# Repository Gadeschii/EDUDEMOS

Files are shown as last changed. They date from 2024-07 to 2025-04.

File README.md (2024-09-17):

# Arduino Temperature, Humidity, Light, and Voltage Control Project

This Arduino project reads temperature and humidity values, controls LEDs based on temperature, uses Light Dependent Resistors (LDRs) to control a servo motor, and measures the voltage of a DC
## Components Used

- ESP32 Board
- Temperature and Humidity Sensor (e.g., DHT11/DHT22)
- LEDs (3 different colors for Cold, Good, and Heat indicators)
- Light Dependent Resistors (LDRs)
- Servo Motor
- Adafruit IO for data logging

## Pin Configuration

- `ledPin1Cold`: Pin connected to the LED indicating cold temperature.
- `ledPin2Good`: Pin connected to the LED indicating good temperature.
- `ledPin3Heat`: Pin connected to the LED indicating high temperature.
- `ldrPin1`: Pin connected to the first LDR.
- `ldrPin2`: Pin connected to the second LDR.
- `myServo`: Pin connected to the servo motor.

## Code Explanation
## Method Explanations

### setup()

Initializes the serial communication, sets up the WiFi connection, OTA updates, DHT sensor, LEDs, and servo motor. It also creates FreeRTOS tasks for reading sensor data and voltage.

### loop()

Handles OTA updates and maintains the connection to Adafruit IO.

### readVoltage()

Reads the voltage from a DC motor using a voltage sensor, converts it to microvolts, and sends the data to Adafruit IO. It takes multiple readings to reduce noise and applies a minimum threshold to filter out noise.

### readSensorTask1(void * parameter)

A FreeRTOS task that periodically reads and processes temperature and humidity data from the DHT sensor. It sends the data to Adafruit IO and controls the LEDs based on the temperature.

### readSensorTask2(void * parameter)

A FreeRTOS task that periodically reads values from two LDRs, calculates the difference, and adjusts the servo motor based on the light difference. It also sends the average LDR values to Adafruit IO.

### readVoltageTask(void * parameter)

A FreeRTOS task that periodically reads and processes the voltage from a DC motor. It sends the voltage data to Adafruit IO.

### setupWiFi()

Connects the ESP32 to a WiFi network and maintains the connection to Adafruit IO.

### setupOTA()

Initializes ArduinoOTA for over-the-air updates and defines OTA event handlers.

### handleOTA()

Handles OTA updates by calling `ArduinoOTA.handle()`.

### setupDHT()

Initializes the DHT sensor.

### setupLEDsAndServo()

Sets up the pins for the LEDs and attaches the servo motor to its pin.

### updateSensorData()

Reads temperature and humidity values from the DHT sensor, sends the data to Adafruit IO, and controls the LEDs based on the temperature.

### updateLDRAndServo()

Reads values from two LDRs, calculates the difference, adjusts the servo motor based on the light difference, and sends the average LDR values to Adafruit IO.

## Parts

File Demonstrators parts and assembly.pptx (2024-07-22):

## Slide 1

GRADO EN INGENIERÍA EN DISEÑO INDUSTRIAL
Y DESARROLLO DE PRODUCTOS

Proyecto ERASMUS +

EDUcating through Sustainable DEMOnstrators

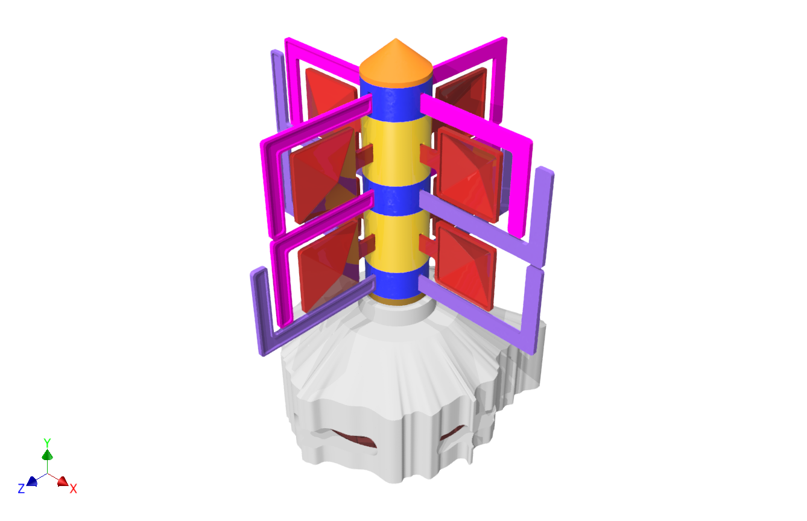
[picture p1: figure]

TRABAJO DE FIN DE GRADO
26 DE JUNIO DE 2024

Autora: Patricia Er López Marrero
Tutor 1: Pedro Manuel Hernández Castellano
Tutora 2: Annabella Narganes Pineda

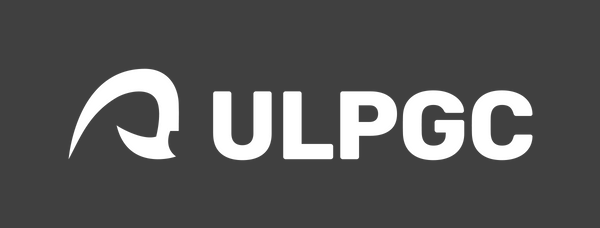
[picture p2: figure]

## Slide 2

1

2

3.5

4

5

Wind Demonstartor

33 pieces

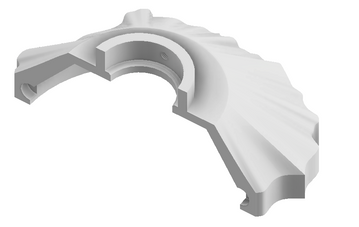
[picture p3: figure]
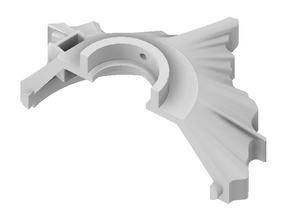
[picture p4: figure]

x2

x3

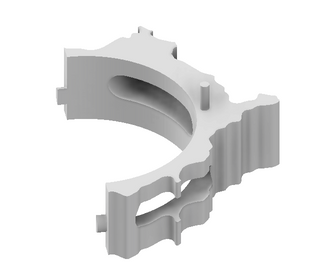
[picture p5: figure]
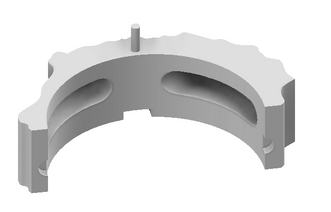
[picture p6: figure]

Cylinders

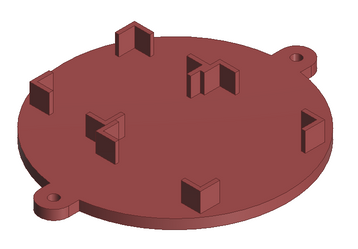
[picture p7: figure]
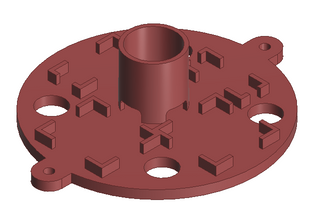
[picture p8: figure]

x8

x6

x6

Base with electronics

Blades


217 mm

259 mm

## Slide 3

Assembly


Base assembly

Cylinders assembly

Wood joints

Blades - cylinders assembly

Top view

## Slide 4

1


166 mm

2

3.5

4

5

Water + Solar Demonstrator

21 pieces


Base with electronics

Solar parts

x8


x2

x2

Water parts

250 mm

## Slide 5

Assembly

Condensation


Solar parts assembly

Cylinders assembly


Leaf - cylinder assembly

Top view

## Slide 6

Prototypes with electronics

Combine


Half section view of the base


Bearing

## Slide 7

Other element specifications

Bearing ZZ type

exterior Ø 40 mm

interior Ø 17 mm

Height 12 mm

1 unit


Wood joints

Ø 8 mm

Height 40 mm

3 units

Aluminum foil tape


1 unit

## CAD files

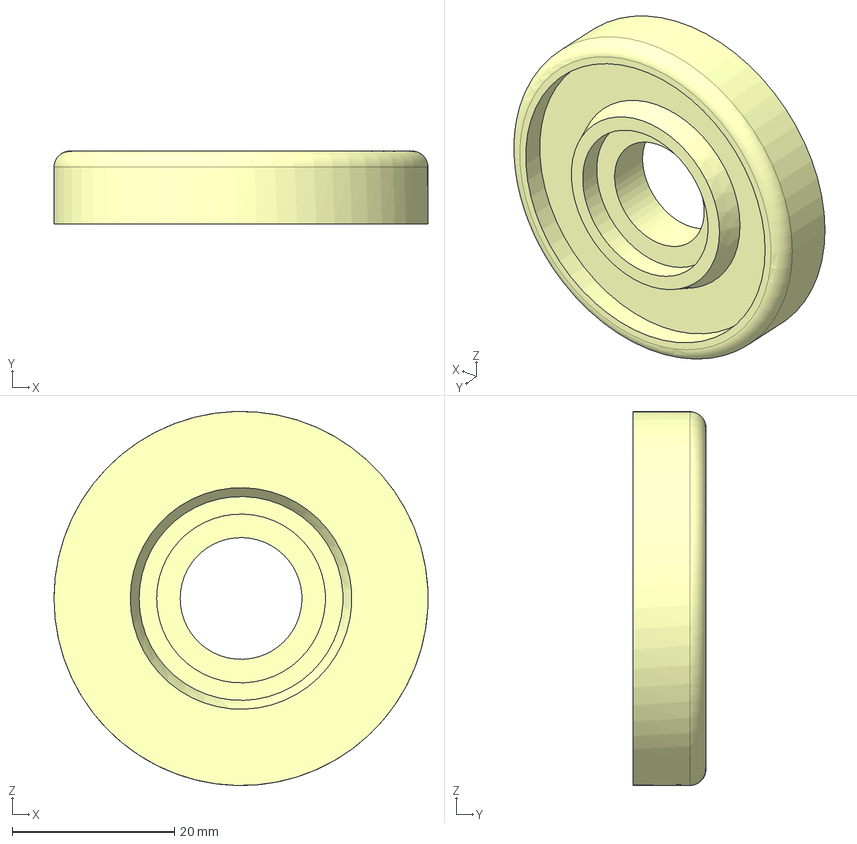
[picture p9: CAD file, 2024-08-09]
3d-files/stp-files/Water static disc_V2_x2.stp
46.1 x 9.00 x 46.1 mm

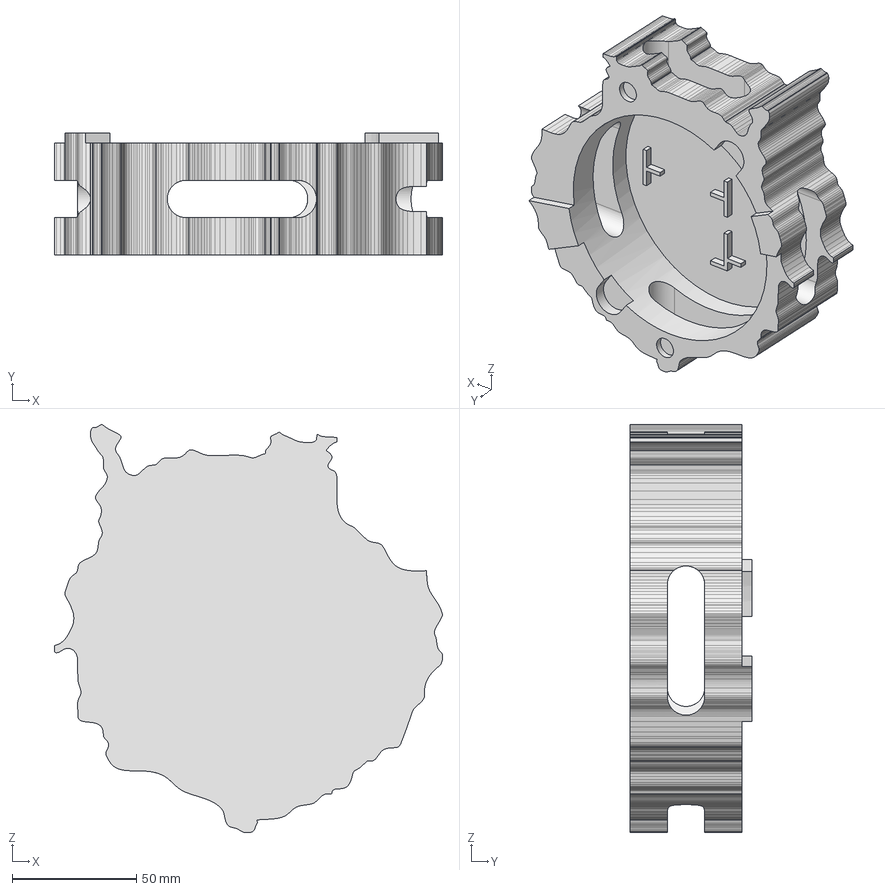
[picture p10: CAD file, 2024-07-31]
3d-files/stp-files/Base_V3_x1.stp
156.1 x 49.0 x 164.1 mm

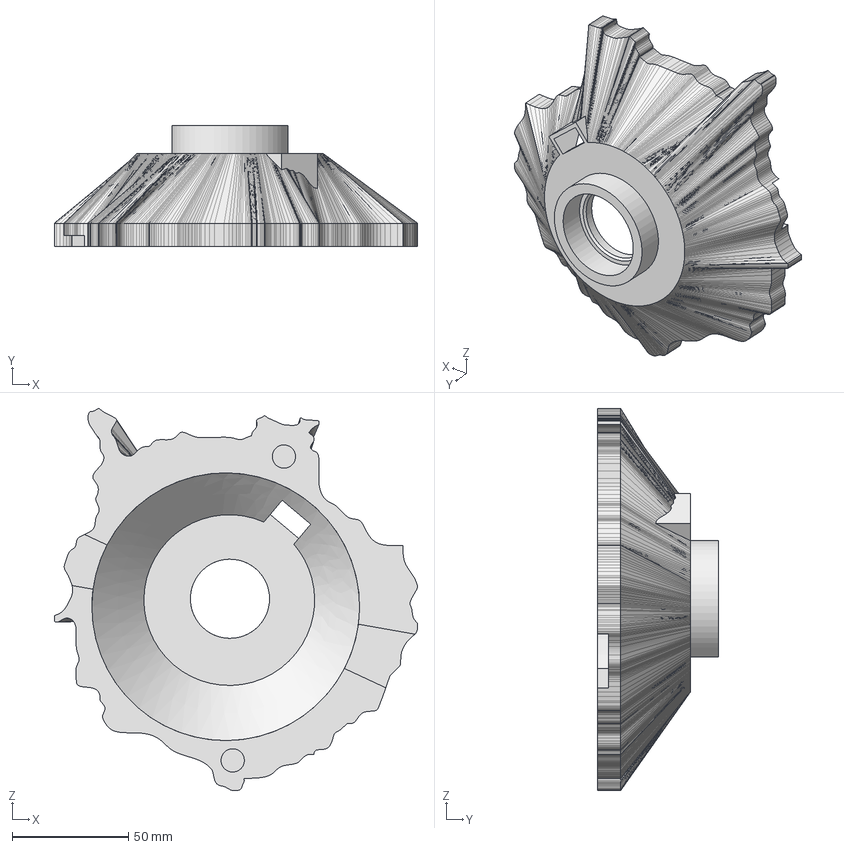
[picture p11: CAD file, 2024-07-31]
3d-files/stp-files/Base top_V3_x1.stp
156.1 x 52.0 x 164.1 mm

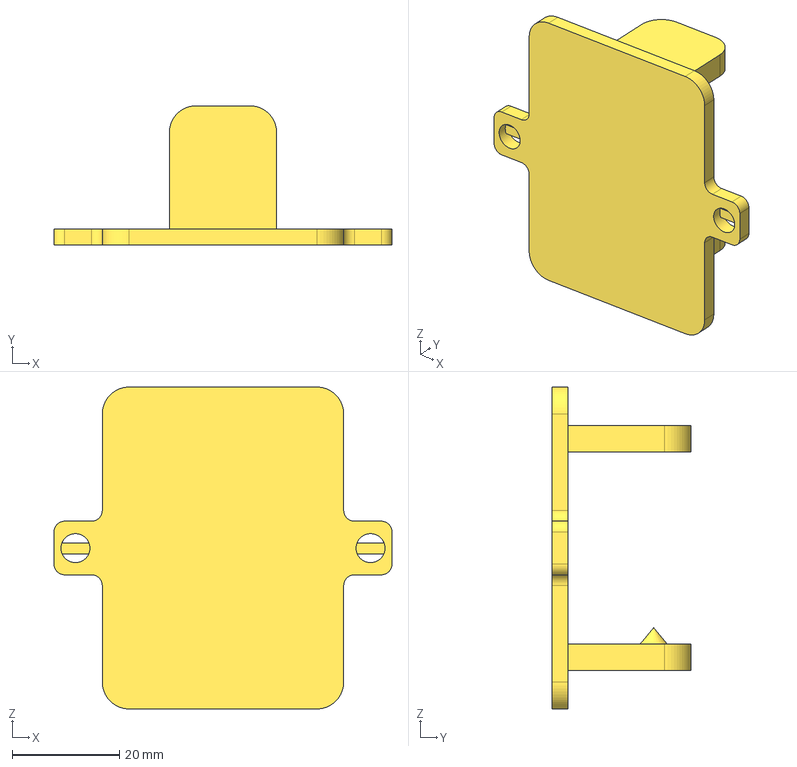
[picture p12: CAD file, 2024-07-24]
3d-files/stp-files/Solar panel spin_V2_x1.stp
63.0 x 26.0 x 60.0 mm

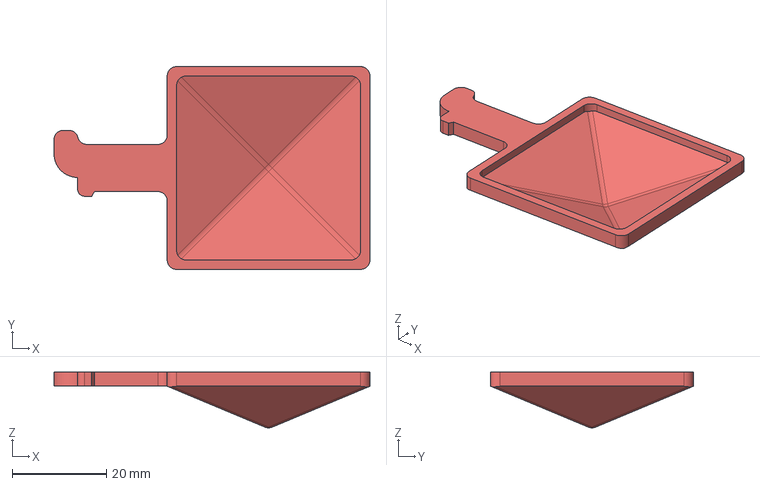
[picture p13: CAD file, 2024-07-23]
3d-files/stp-files/Square blade_x8.stp
67.0 x 43.0 x 11.8 mm

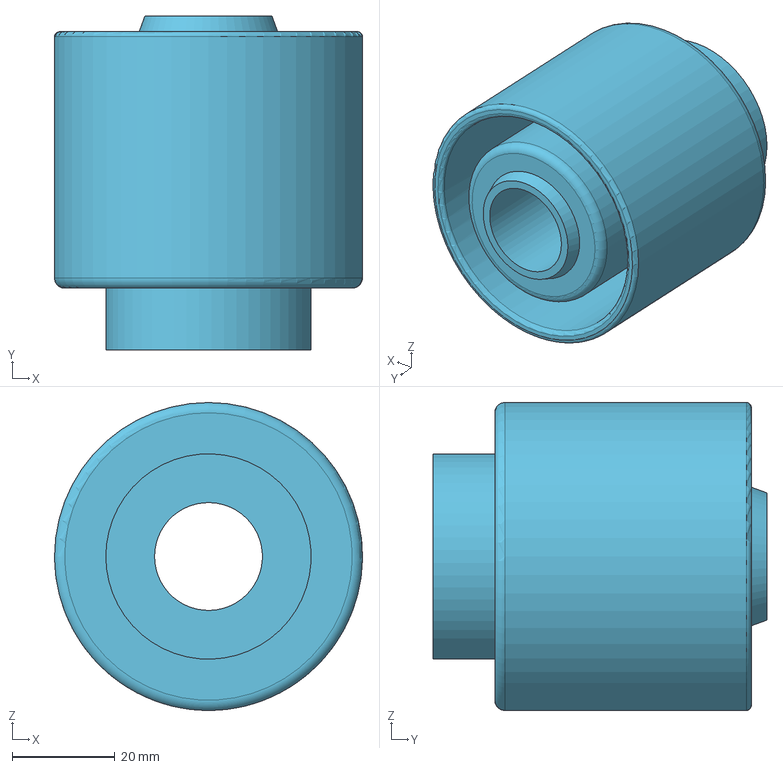
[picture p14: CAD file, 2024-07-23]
3d-files/stp-files/Water container_x1.stp
60.0 x 65.0 x 60.0 mm

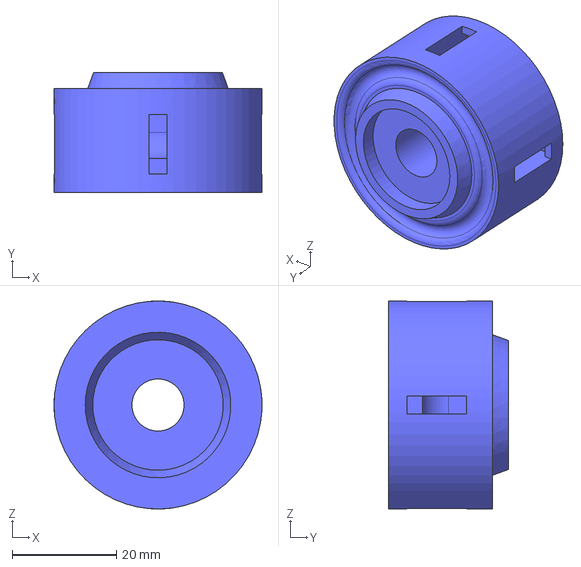
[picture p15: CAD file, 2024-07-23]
3d-files/stp-files/Small disc_x3.stp
40.0 x 23.0 x 40.0 mm

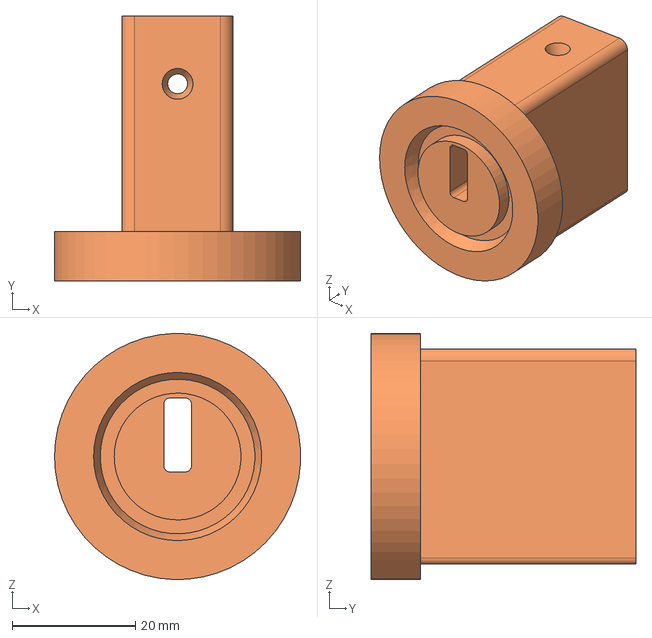
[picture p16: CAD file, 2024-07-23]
3d-files/stp-files/Solar static disc_x1.stp
40.0 x 43.0 x 40.0 mm

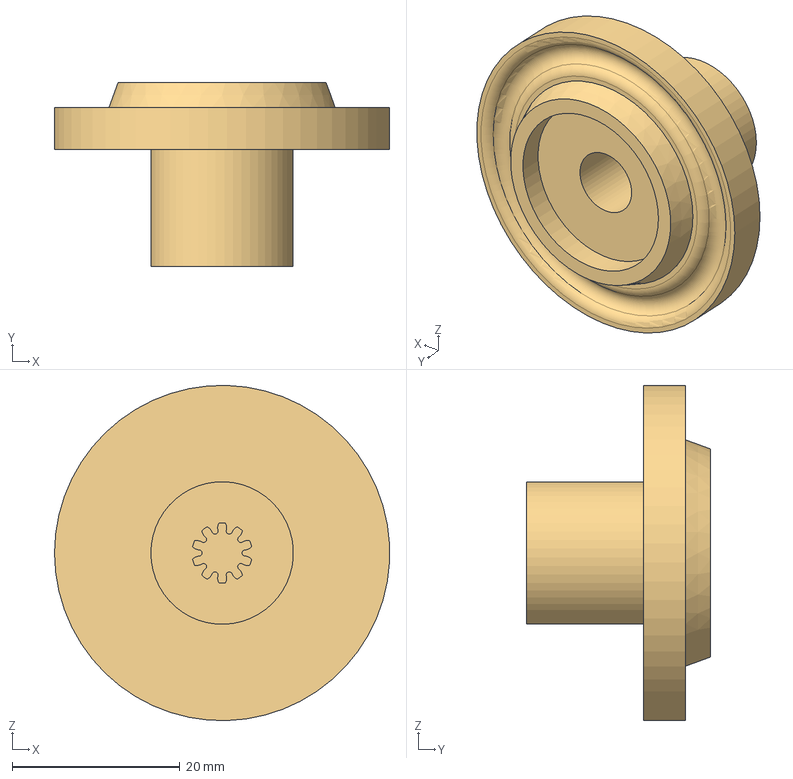
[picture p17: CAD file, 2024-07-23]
3d-files/stp-files/Wind bearing disc_x1.stp
40.0 x 22.0 x 40.0 mm

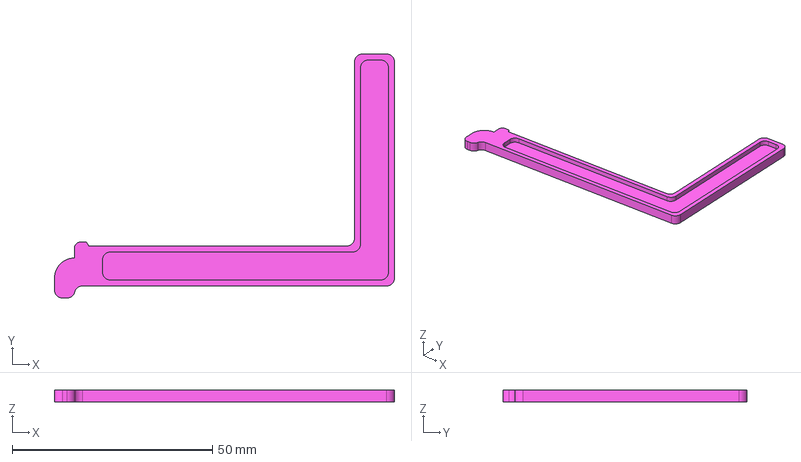
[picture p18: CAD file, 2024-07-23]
3d-files/stp-files/Small L blade_x6.stp
85.0 x 61.0 x 3.00 mm

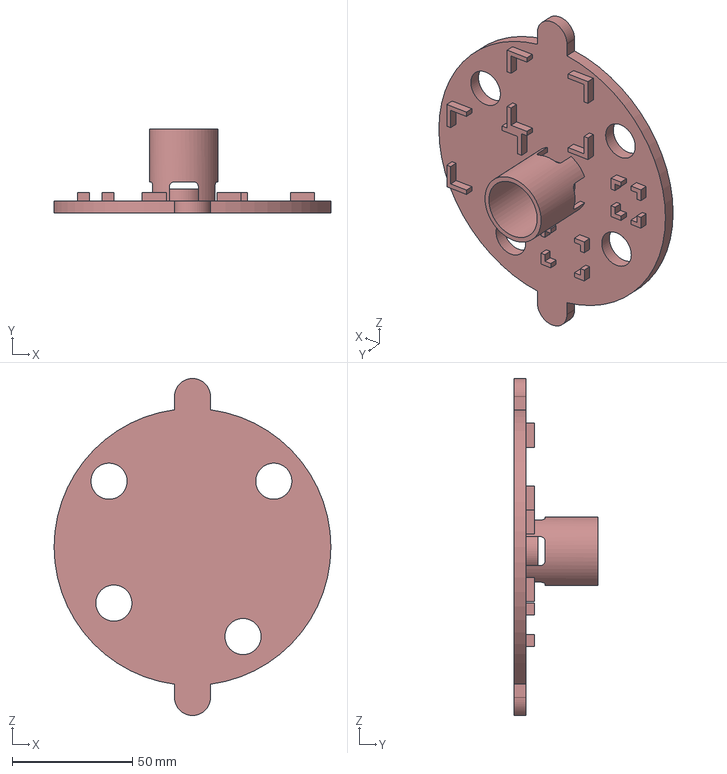
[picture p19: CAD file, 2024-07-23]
3d-files/stp-files/Base middle_x1.stp
115.0 x 35.0 x 140.0 mm

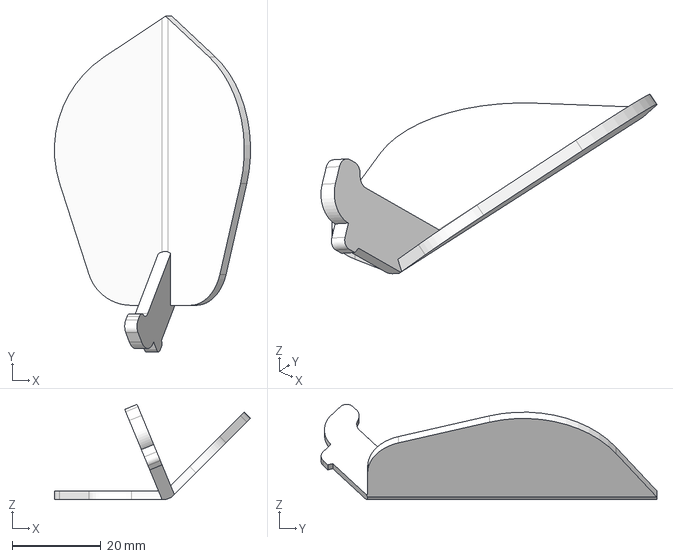
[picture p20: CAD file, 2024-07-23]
3d-files/stp-files/Leaf_x8.stp
44.1 x 75.4 x 21.4 mm

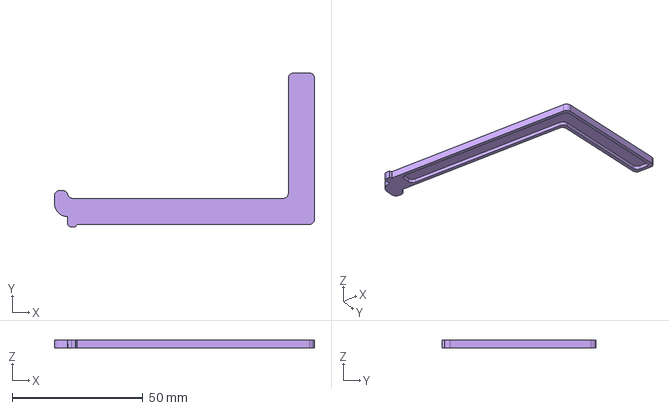
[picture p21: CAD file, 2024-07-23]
3d-files/stp-files/Big L blade_x6.stp
99.5 x 59.0 x 3.00 mm

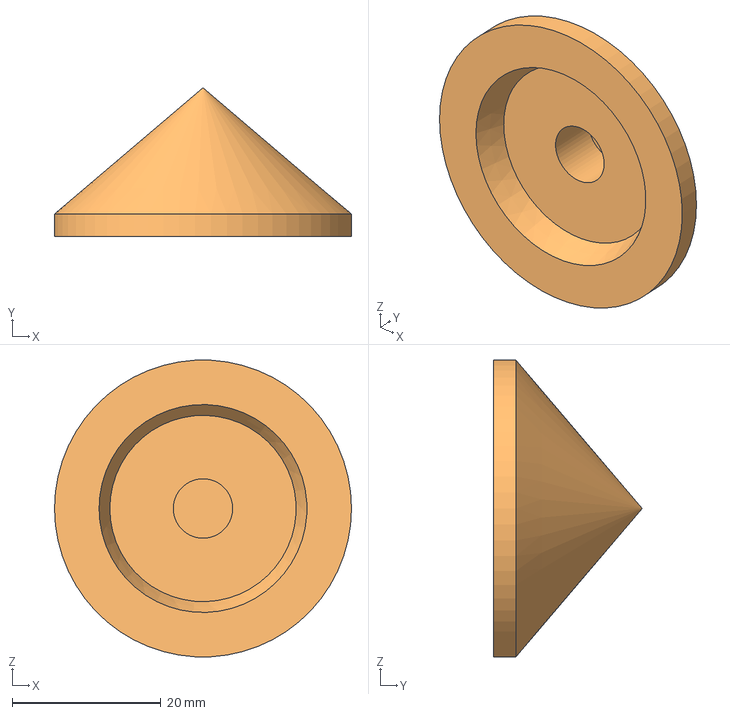
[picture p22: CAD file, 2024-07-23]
3d-files/stp-files/Top_x1.stp
40.0 x 20.0 x 39.9 mm

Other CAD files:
3d-files/stp-files/Big disc_x2.stp
3d-files/stp-files/Base_V2_x1.stp
3d-files/stp-files/Base top_V2_x1.stp
3d-files/stp-files/Base_x1.stp
3d-files/stp-files/Base top_x1.stp
3d-files/stp-files/Solar panel spin_x1.stp
3d-files/stp-files/Water static disc_x2.stp

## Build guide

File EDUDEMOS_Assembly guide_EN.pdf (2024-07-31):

# 3 x 1 Convertible demonstrator

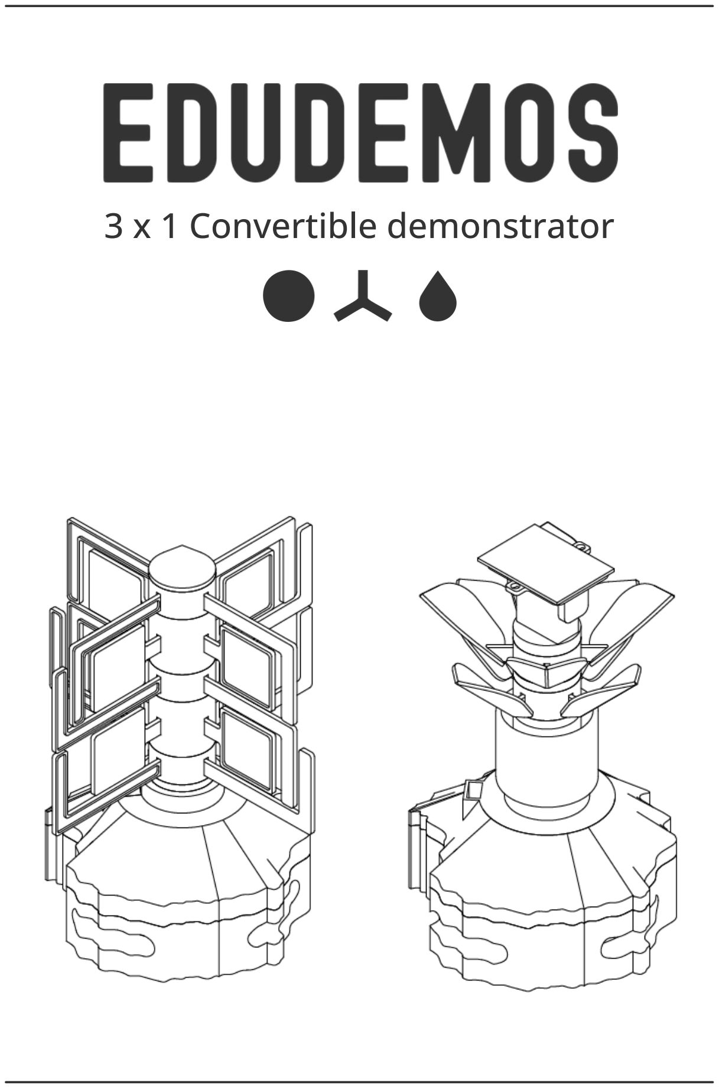
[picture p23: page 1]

# 3x1 Demonstrator

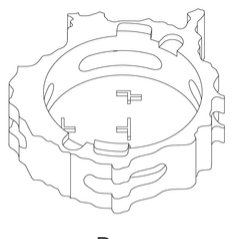
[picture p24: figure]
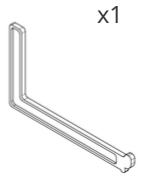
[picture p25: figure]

Bearing | Wood joints
x1 | x3

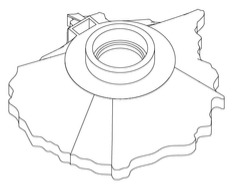
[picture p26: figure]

Big L blade | Square blade | Small L blade
x6 | x8 | x6

Leaf
x8

## Elements

Base | Middle base | Top base
x1 | x1 | x1
Big disc | Small disc Bearing disc | Top
x2 | x3 | x1 | x1

Static disc
x2

Water container
x1

Solar spin
x1

Solar disc
x1

## Total 47 elements

# Wind demonstrator

## Assembly guide

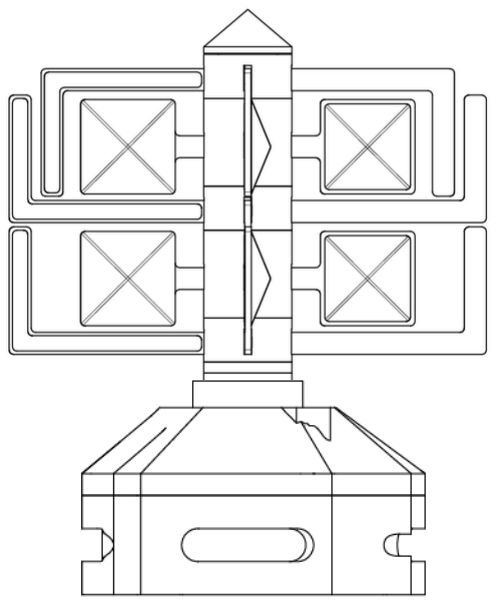
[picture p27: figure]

# Wind demonstrator

## Elements

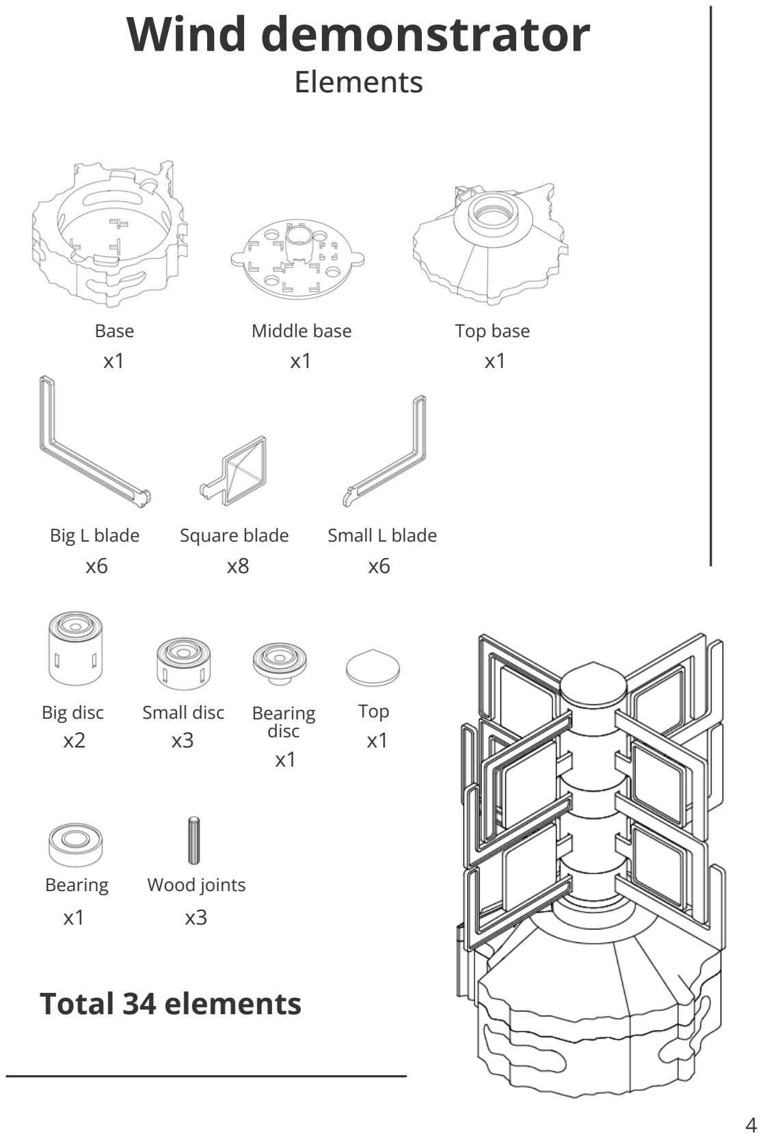
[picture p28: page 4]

Bearing | Wood joints
Big L blade | Square blade | Small L blade
Base | Middle base | Top base
x1 | x1 | x1
x6 | x8 | x6
Big disc | Small disc Bearing disc

Top
x2 | x3 x1

x1

x1 | x3

## Total 34 elements

# Wind demonstrator

## Core assembly

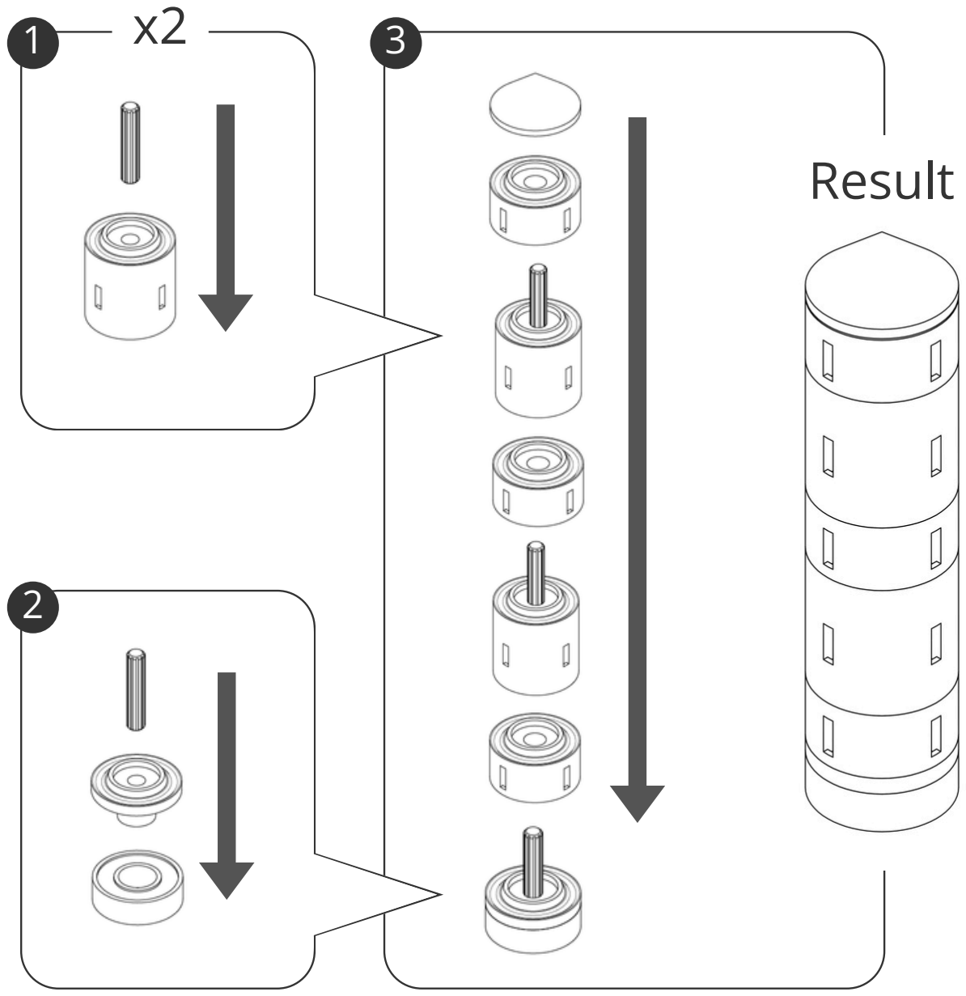
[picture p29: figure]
Result

The two big discs should move together, while each small discs should move individually.
If needed, take out a little bit the big discs from the wood joints in order to reduce friction.

6

## Blades assembly

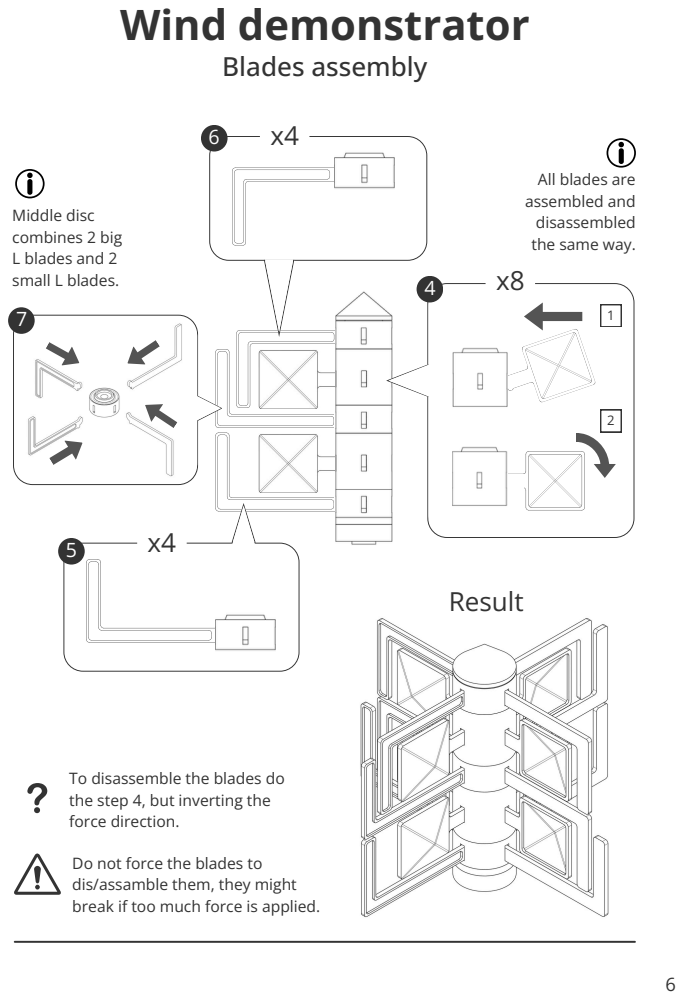
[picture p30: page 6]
Wind demonstrator; Middle disc combines 2 big L blades and 2 small L blades.; Result

All blades are
assembled and
disassembled
the same way.

To disassemble the blades do
the step 4, but inverting the
force direction.

Do not force the blades to
dis/assamble them, they might
break if too much force is applied.

# Wind demonstrator

## Base assembly

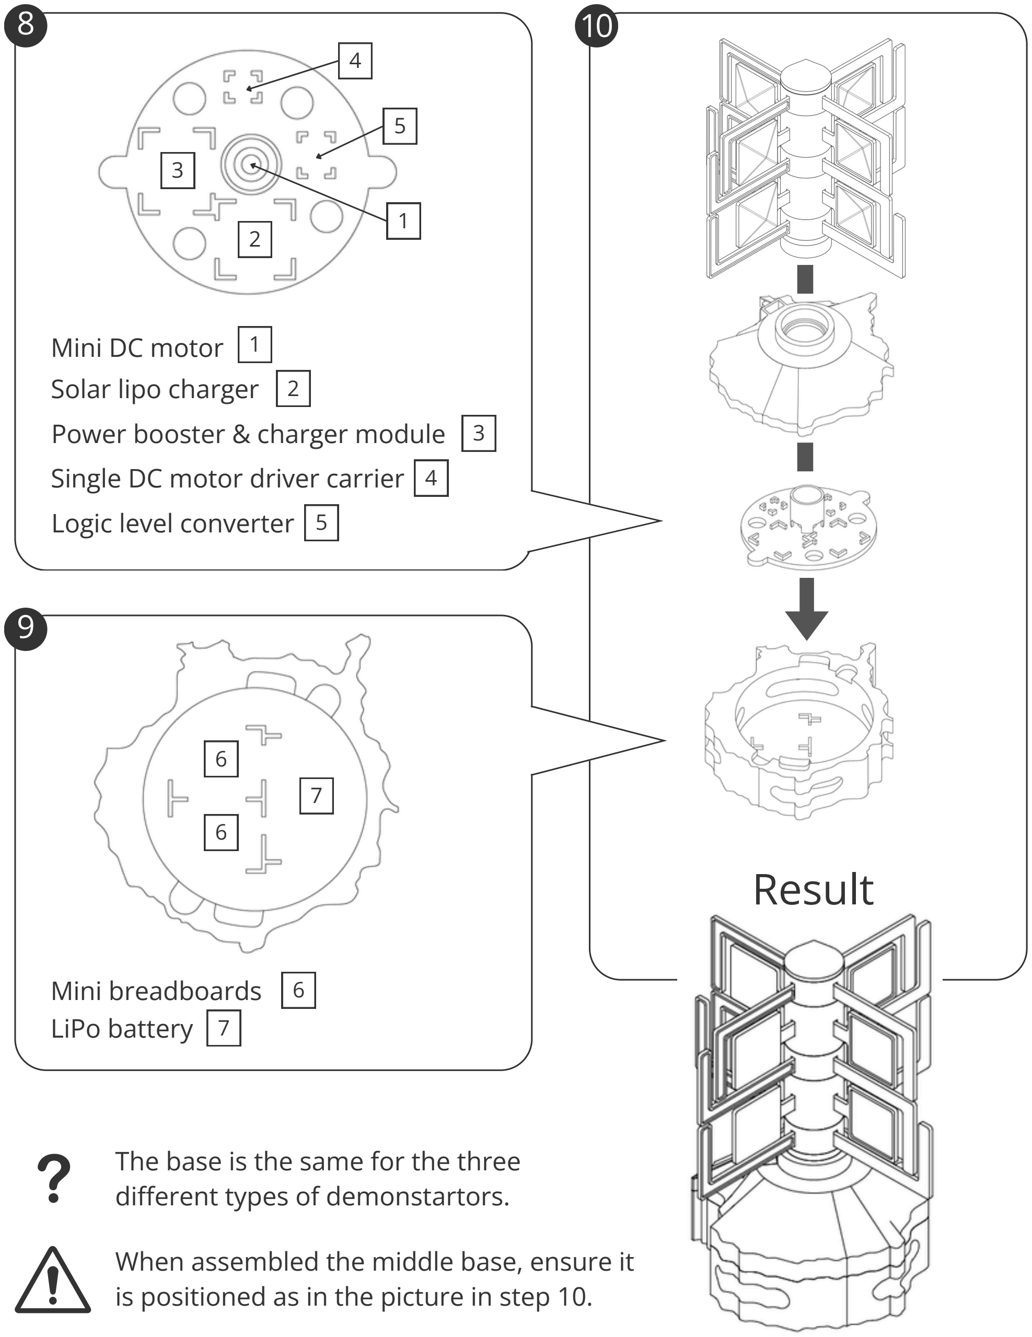
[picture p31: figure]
Mini breadboards LiPo battery; Mini DC motor; The base is the same for the three different types of demonstartors.; Power booster & charger module; Solar lipo charger; Logic level converter; Single DC motor driver carrier; Result

When assembled the middle base, ensure it is positioned as in the picture in step 10.

# Solar + Water demonstrator

## Assembly guide

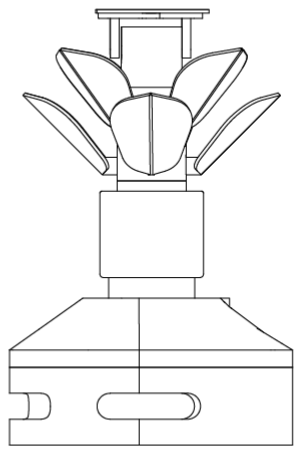
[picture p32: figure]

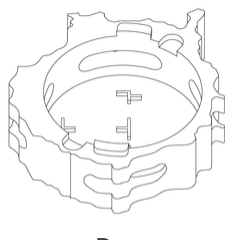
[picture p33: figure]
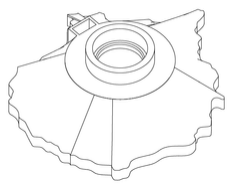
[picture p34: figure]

Base | Middle base | Top base
x1 | x1 | x1

# Solar + Water demonstrator

## Elements

Small disc
x3

Water container
x1

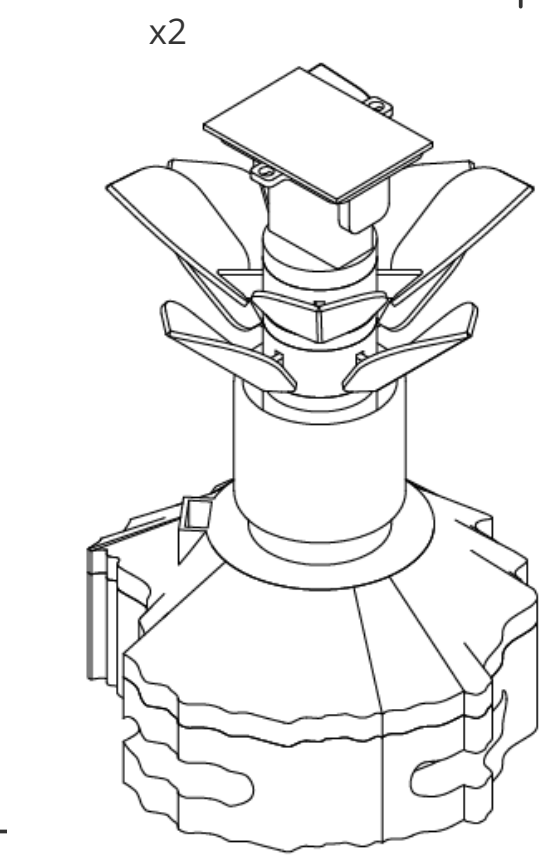
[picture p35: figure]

Solar spin
x1

Solar disc
x1

Leaf
x8

Static disc

Water demonstrator

Solar demonstrator

## Total 19 elements

## Core assembly

1 | 3

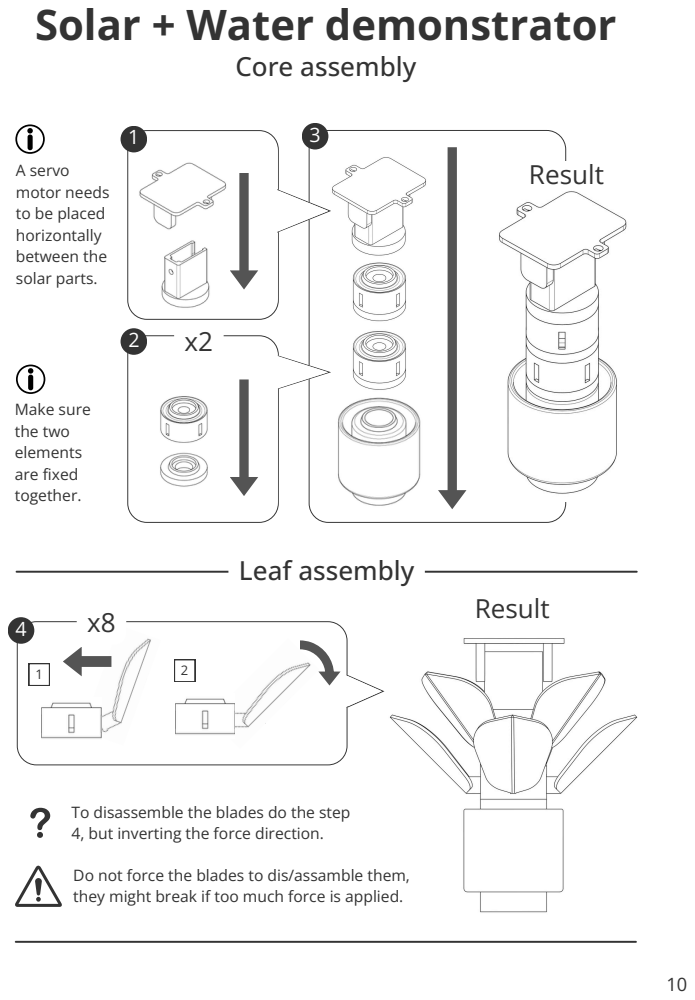
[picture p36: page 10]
Result; Leaf assembly; Make sure the two elements are fixed together.

Solar + Water demonstrator

A servo
motor needs
to be placed
horizontally
between the
solar parts.

To disassemble the blades do the step
4, but inverting the force direction.

Do not force the blades to dis/assamble them,
they might break if too much force is applied.

5

## Base assembly

See page 7 for the base assembly instructions.

# Solar + Water demonstrator

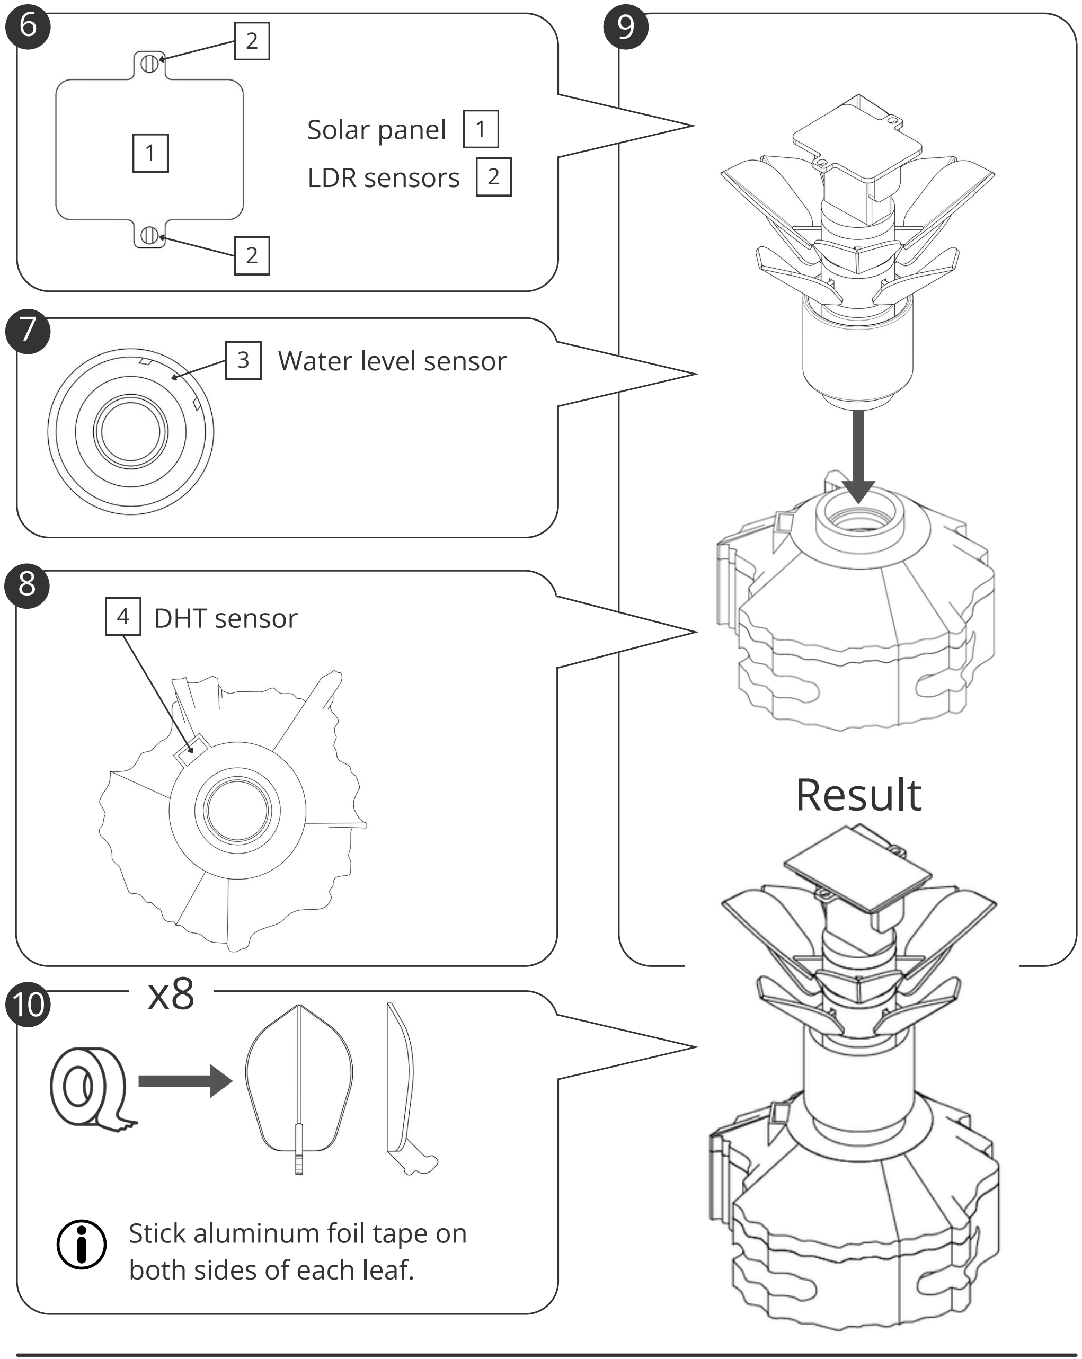
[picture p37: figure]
DHT sensor; Solar panel; Stick aluminum foil tape on both sides of each leaf.; Result; LDR sensors; Water level sensor

## Personalise your own demonstrator

# What else can you imagine?

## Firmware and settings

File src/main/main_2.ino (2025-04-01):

/*                                                                                                           *
 *  Thank you for building EduDemoS!                                                                         *
 *                                                                                                           *
 *  This file is part of the EduDemoS Project and is licensed under the Creative Commons Attribution         *
 *  NonCommercial ShareAlike 4.0 International license (CC BY-NC-SA 4.0). For full license details, see the  *
 *  license.txt file or visit https://creativecommons.org/licenses/by-nc-sa/4.0/                             *     
 *                                                                                                           *
 *  EduDemoS is co-funded by the European Union. You can find more information at edudemos.eu                *                                                         
 *                                                                                                           *
 *  +-----------------------------------------------------------------------------------------------------+  *            
 */

//include the necesary libraries
#include <WiFi.h>
#include <WiFiClient.h>
#include <HTTPClient.h>
#include <ArduinoJson.h>
#include "AdafruitIO_WiFi.h"
#include "DHT.h"
#include <ESP32Servo.h>
#include <ArduinoOTA.h>
//#include "config.h"

// Pin definitions and constants
#define DHTPIN 32
#define DHTTYPE DHT11
#define ledPin1Cold 5
#define ledPin2Good 18
#define ledPin3Heat 19
#define ldrPin1 34
#define ldrPin2 35
#define servoPin 25
#define DcMotorPin 39
#define SolarPin 36
#define SENSOR_INTERVAL_10_SEC 10000
#define OFFSET 550
#define OFFSETLDR 300 //Difference between LDR1 and LDR2, (each case are different), look for yor personal value

/************************ Adafruit IO Config *******************************/
#define IO_USERNAME "IO_USERNAME"
#define IO_KEY "IO_KEY"

/******************************* WIFI **************************************/
#define WIFI_SSID "WIFI_SSID"
#define WIFI_PASS "WIFI_PASS"

WiFiServer telnetServer(23); 
WiFiClient telnetClient;

// Voltage divider resistances definitions
const float R1 = 1000.0; // 1kΩ resistor
const float R2 = 1000.0; // 1kΩ resistor

// Global variables
DHT dht(DHTPIN, DHTTYPE);
Servo myServo;

// Variables to store LDR sensor readings
int ldrValue1 = 0;
int ldrValue2 = 0;
int averageLdrValue = 0;

// Variables to store water sensor readings
const int WaterSensorPin = 39; // // Analog Value from VN PIN
int sensorValue = 0; // Analog Value filter

// Servo configuration variables
int servoPos = 100;  // Initial servo position in the middle (90 degrees)
int servoStep = 10;  // Servo movement increment/decrement
int tolerance = 150; // Tolerance to avoid small movements

AdafruitIO_WiFi io(IO_USERNAME, IO_KEY, WIFI_SSID, WIFI_PASS);
AdafruitIO_Feed *temperature = io.feed("temperature");
AdafruitIO_Feed *humidity = io.feed("humidity");
AdafruitIO_Feed *ldrFeed = io.feed("ldr");
//AdafruitIO_Feed *ldr1Feed = io.feed("ldr1Feed");
//AdafruitIO_Feed *ldr2Feed = io.feed("ldr2Feed");
AdafruitIO_Feed *waterLevelFeed = io.feed("waterLevel");
AdafruitIO_Feed *microvoltsMotorDcFeed = io.feed("microvoltsMotorDc");
AdafruitIO_Feed *microvoltsSolarFeed = io.feed("microvoltsSolar");
AdafruitIO_Feed *ledHighFeed =  io.feed("ledHighFeed");
AdafruitIO_Feed *ledGoodFeed =  io.feed("ledGoodFeed");
AdafruitIO_Feed *ledColdFeed =  io.feed("ledColdFeed");
AdafruitIO_Feed *wifiFeed =  io.feed("wifiFeed");
float lastMicrovolts = 0;

void setup() {
  Serial.begin(115200); // Start serial communication at 115200 baud rate
  analogReadResolution(12); // ESP32 has a 12-bit ADC
  analogSetAttenuation(ADC_11db); // Set attenuation for higher sensitivity
  pinMode(4, INPUT);

  //setupWiFi(); // Setup WiFi connection
  //setupOTA(); // Setup OTA for remote updates
  setupDHT(); // Setup DHT sensor
  setupLEDsAndServo(); // Setup LED pins and servo

  // Create tasks
  xTaskCreatePinnedToCore(
    readSensorTask1,   // Task function
    "ReadSensorTask1", // Name of the task
    4096,             // Stack size
    NULL,              // Task input parameter
    1,                 // Priority of the task
    NULL,              // Task handle
    0                  // Core where the task should run
  );

  xTaskCreatePinnedToCore( 
    readSensorTask2,   // Task function
    "ReadSensorTask2", // Name of the task
    4096,             // Stack size
    NULL,              // Task input parameter
    1,                 // Priority of the task
    NULL,              // Task handle
    1                  // Core where the task should run
  );

  xTaskCreatePinnedToCore(
    readSensorTask3,   // Task function
    "ReadSensorTask3", // Name of the task
    4096,             // Stack size
    NULL,              // Task input parameter
    1,                 // Priority of the task
    NULL,              // Task handle
    1                  // Core where the task should run
  );

  xTaskCreatePinnedToCore(
    readDcMotorVoltageTask,   // Task function
    "readDcMotorVoltageTask", // Name of the task
    4096,             // Stack size
    NULL,              // Task input parameter
    1,                 // Priority of the task
    NULL,              // Task handle
    1                  // Core where the task should run
  );

  xTaskCreatePinnedToCore(
    readSolarVoltageTask,   // Task function
    "readSolarVoltageTask", // Name of the task
    4096,             // Stack size
    NULL,              // Task input parameter
    1,                 // Priority of the task
    NULL,              // Task handle
    1                  // Core where the task should run
  );
}

void loop() {
  //handleOTA(); // Handle OTA updates
  //io.run(); // Maintain connection to Adafruit IO
}

void setupWiFi() {
  int retries = 0;
  const int maxRetries = 5;

  WiFi.begin(WIFI_SSID, WIFI_PASS);
  Serial.print("Connecting to WiFi");

  while (WiFi.status() != WL_CONNECTED && retries < maxRetries) {
    delay(1000);
    Serial.print(".");
    retries++;
  }

  if (WiFi.status() == WL_CONNECTED) {
    Serial.println("\nConnected to WiFi");
    // Send microvolts to Adafruit IO
    wifiFeed->save(WIFI_SSID);
  } else {
    Serial.println("\nWiFi connection failed. Restarting...");
    ESP.restart();
  }

  connectToAdafruitIO();
}

void connectToAdafruitIO() {
  Serial.print("Connecting to Adafruit IO");
  io.connect();

  int retries = 0;
  const int maxRetries = 5;

  while (io.status() < AIO_CONNECTED && retries < maxRetries) {
    Serial.print(".");
    delay(500);
    retries++;
  }

  if (io.status() < AIO_CONNECTED) {
    Serial.println("\nFailed to connect to Adafruit IO. Restarting...");
    ESP.restart();
  }

  Serial.println("\nConnected to Adafruit IO");
}

void setupOTA() {
  // Start telnet server
  telnetServer.begin();
  telnetServer.setNoDelay(true);
  // Initialize ArduinoOTA for over-the-air updates
  ArduinoOTA.setHostname("ESP32-OTA");
  ArduinoOTA.setPassword("admin"); // Uncomment to set a password for OTA updates
  // Define OTA event handlers
  ArduinoOTA.onStart([]() {
    String type;
    if (ArduinoOTA.getCommand() == U_FLASH) {
      type = "sketch";
    } else { // U_SPIFFS
      type = "filesystem";
    }
    Serial.println("Start updating " + type);
  });
  ArduinoOTA.onEnd([]() {
    Serial.println("\nOTA Update Finished");
  });
  ArduinoOTA.onProgress([](unsigned int progress, unsigned int total) {
    Serial.printf("Progress: %u%%\r", (progress / (total / 100)));
  });
  ArduinoOTA.onError([](ota_error_t error) {
    Serial.printf("Error[%u]: ", error);
    if (error == OTA_AUTH_ERROR) {
      Serial.println("Auth Failed");
    } else if (error == OTA_BEGIN_ERROR) {
      Serial.println("Begin Failed");
    } else if (error == OTA_CONNECT_ERROR) {
      Serial.println("Connect Failed");
    } else if (error == OTA_RECEIVE_ERROR) {
      Serial.println("Receive Failed");
    } else if (error == OTA_END_ERROR) {
      Serial.println("End Failed");
    }
  });
  ArduinoOTA.begin(); // Start the OTA service
  Serial.println("OTA Ready");
}

void handleOTA() {
  ArduinoOTA.handle(); // Handle OTA updates

  //check if there are new client
  // Verificar si hay un nuevo cliente telnet
  if (telnetServer.hasClient()) {
    if (!telnetClient || !telnetClient.connected()) {
      if (telnetClient) telnetClient.stop();
      telnetClient = telnetServer.available();
      Serial.println("New Telnet client connected");
    } else {
      telnetServer.available().stop();
    }
  }

  //Send data to the telnet client server
  if (telnetClient && telnetClient.connected()) {
    while (Serial.available()) {
      telnetClient.write(Serial.read());
    }
    while (telnetClient.available()) {
      Serial.write(telnetClient.read());
    }
  }

}
void setupDHT() {
  dht.begin(); // Start the DHT sensor
}

void setupLEDsAndServo() {
  pinMode(ledPin1Cold, OUTPUT);
  pinMode(ledPin2Good, OUTPUT);
  pinMode(ledPin3Heat, OUTPUT);
  // Attach the servo to the corresponding pin
  myServo.attach(servoPin);

  // Set the servo to the initial position (90 degrees, in the middle)
  myServo.write(servoPos);
}

void readSensorTask1(void * parameter) {
  for (;;) {
    Serial.println("----------------------- Measured Temperature / Humidity -----------------------  ");
    updateSensorData(); // Read and process sensor data 
    vTaskDelay(SENSOR_INTERVAL_10_SEC / portTICK_PERIOD_MS); // Delay for 5 minutes
  }
}

void readSensorTask2(void * parameter) {
  for (;;) {
    Serial.println("----------------------------- Measured LDR and Servo -----------------------------  ");
    updateLDRAndServo(); // Read LDR values and control servo
    vTaskDelay(SENSOR_INTERVAL_10_SEC / portTICK_PERIOD_MS); // Delay for 10 seconds
  }
}

void readSensorTask3(void * parameter) {
  for (;;) {
    Serial.println("----------------------------- Measured Water % -----------------------------  ");
    updateWater(); // Read LDR values and control servo
    vTaskDelay(SENSOR_INTERVAL_10_SEC / portTICK_PERIOD_MS); // Delay for 10 seconds
  }
}

void readSolarVoltageTask(void * parameter) {
  for (;;) {
    Serial.println("----------------------------- Measured Solar (V) ----------------------------  ");
    readSolarVoltage(); // Read and process voltage
    vTaskDelay(SENSOR_INTERVAL_10_SEC / portTICK_PERIOD_MS); // Delay for 10 seconds
  }
}

void readDcMotorVoltageTask(void * parameter) {
  for (;;) {
    Serial.println("----------------------------- Measured DC Motor (V) ----------------------------  ");
    readDcMotorVoltage(); // Read and process voltage
    vTaskDelay(SENSOR_INTERVAL_10_SEC / portTICK_PERIOD_MS); // Delay for 10 seconds
  }
}


void readDcMotorVoltage() {
  // Take multiple readings to reduce noise
  const int numReadings = 1000;
  unsigned long sum = 0;

  for (int i = 0; i < numReadings; i++) {
    int reading = analogRead(DcMotorPin);
    sum += reading;
  }

  float averageReading = sum / (float)numReadings;
  Serial.print("Average ADC reading: ");
  Serial.println(averageReading);  // Display the average value

  // Calculate voltage
  float voltage = (averageReading / 4095.0) * 3.3;  // For 12-bit ADC (0-4095)
  Serial.print("Measured voltage (V): ");
  Serial.println(voltage);  // Display the measured voltage

  // Adjust for voltage divider
  float inputVoltage = voltage / (R2 / (R1 + R2));

  // Convert to microvolts
  float microvoltsMotorDc = inputVoltage * 1000000.0;
  Serial.print("Input voltage (µV): ");
  Serial.println(microvoltsMotorDc);

  // Apply a minimum threshold to filter noise
  const float threshold = 10.0;  // Threshold in microvolts
  if (microvoltsMotorDc < threshold) {
    microvoltsMotorDc = 0;
  }

  // Check if the microvolts value has changed
  if (microvoltsMotorDc != lastMicrovolts) {
    Serial.print("Measured voltage: ");
    Serial.print(microvoltsMotorDc, 2);  // Display with 2 decimal places
    Serial.println(" µV");

    // Send microvolts to Adafruit IO
    microvoltsMotorDcFeed->save(microvoltsMotorDc);

    // Update the last microvolts value
    lastMicrovolts = microvoltsMotorDc;
  }
}

void readSolarVoltage() {
 int solarVoltagedV = analogRead ( SolarPin); //dV
 int solarVoltage = solarVoltagedV * 10;

  Serial.print("Voltage of Solar Panel: ");
  Serial.println(solarVoltage);  

  // Calculate voltage
  float voltage = (solarVoltage / 4095.0) * 3.3;  // For 12-bit ADC (0-4095)
  Serial.print("Measured voltage (V): ");
  Serial.println(voltage);  // Display the measured voltage

  // Convert to microvolts
  float microvoltsSolar = voltage * 1000000.0;
  Serial.print("Input voltage (µV): ");
  Serial.println(microvoltsSolar);

  // Apply a minimum threshold to filter noise
  const float threshold = 10.0;  // Threshold in microvolts
  if (microvoltsSolar < threshold) {
    microvoltsSolar = 0;
  }

  // Check if the microvolts value has changed
  if (microvoltsSolar != lastMicrovolts) {
    Serial.print("Send voltage: ");
    Serial.print(microvoltsSolar, 2);  // Display with 2 decimal places
    Serial.println(" µV");

    // Send microvolts to Adafruit IO
    microvoltsSolarFeed->save(microvoltsSolar);

    // Update the last microvolts value
    lastMicrovolts = microvoltsSolar;
  }
}

void updateSensorData() {
  // Read values from DHT sensor
  float h = dht.readHumidity();
  float t = dht.readTemperature();

  // Check if readings are valid
  if (isnan(h) || isnan(t)) {
    Serial.println("Failed to read from DHT sensor!");
    return;
  }

  // Send values to Adafruit IO
  temperature->save(t);
  humidity->save(h);

  // Print sensor values
  Serial.print("Temperature: ");
  Serial.print(t);
  Serial.print(" °C, Humidity: ");
  Serial.print(h);
  Serial.println(" %");

  // Example LED control based on temperature
  if (t < 20) {
    digitalWrite(ledPin1Cold, HIGH);
    digitalWrite(ledPin2Good, LOW);
    digitalWrite(ledPin3Heat, LOW); 
     // Send to the corresponding feed (Cold LED)
    ledColdFeed->save(1);  // 1 means the LED is ON
    ledGoodFeed->save(0);  // OFF
    ledHighFeed->save(0);  // OFF
    Serial.println("Cold is HIGH");
    
  } else if (t >= 20 && t < 25) {
    digitalWrite(ledPin1Cold, LOW);
    digitalWrite(ledPin2Good, HIGH);
    digitalWrite(ledPin3Heat, LOW);
    // Send to the corresponding feed (Good LED)
    ledColdFeed->save(0);  // OFF
    ledGoodFeed->save(1);  // ON
    ledHighFeed->save(0);  // OFF
       Serial.println("Good is HIGH");
  } else {
    digitalWrite(ledPin1Cold, LOW);
    digitalWrite(ledPin2Good, LOW);
    digitalWrite(ledPin3Heat, HIGH);
    // Send to the corresponding feed (Heat LED)
    ledColdFeed->save(0);  // OFF
    ledGoodFeed->save(0);  // OFF
    ledHighFeed->save(1);  // ON
    Serial.println("Heat is HIGH");
  }
}

void updateWater(){
  sensorValue = analogRead(WaterSensorPin); // Read the value from the soil moisture sensor
  //Check watersensor calibration first
  if (sensorValue >= 2000) { //These value represents de max value given 
    sensorValue = 1980; //This value would return a 99% value
  }
  float waterlevel = (sensorValue*100)/2000 ; //Calculation to return the %
  
  Serial.print("Water level: "); // Print value in serial monitor
  Serial.print(waterlevel); // Print value in serial monitor
  Serial.println(" %"); // Print value in serial monitor

  // Send the average value to Adafruit IO
  waterLevelFeed->save(waterlevel);
}

void updateLDRAndServo() {
  // Read LDR values
  ldrValue1 = analogRead(ldrPin1) ;
  ldrValue2 = analogRead(ldrPin2) + OFFSETLDR;

  // Invert readings so low values mean darkness and high values mean light
 
  averageLdrValue = (ldrValue1 + ldrValue2) / 2;

  // Print readings for debugging
  Serial.print("LDR 1: ");
  Serial.print(ldrValue1);
  Serial.print(" | LDR 2: ");
  Serial.println(ldrValue2);
  Serial.print("Average LDR: ");
  Serial.println(averageLdrValue);

  // Send the average value to Adafruit IO
  ldrFeed->save(averageLdrValue);
  //ldr1Feed-> save (ldrValue1);
  //ldr2Feed -> save (ldrValue2);

  // Compare LDR values and move the servo based on the difference
  if (ldrValue1 > ldrValue2 + tolerance) {
    if (servoPos > 0) {
      servoPos -= servoStep;  // Move the servo to the left
      Serial.println("Moving left");
    }
  } else if (ldrValue2 > ldrValue1 + tolerance) {
    if (servoPos < 180) {
      servoPos += servoStep;  // Move the servo to the right
      Serial.println("Moving right");
    }
  }

  // Ensure the servo stays within the [0, 180] range
  servoPos = constrain(servoPos, 0, 180);

  // Move the servo to the new position only if it has changed
  myServo.write(servoPos);

  // Print the servo angle
  Serial.print("Servo angle: ");
  Serial.println(servoPos);

  // Pause to give the servo time to move
  delay(30);  // Increase the delay for more response time for the servo
}

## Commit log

2024-07-22 - Setting folder - Wifi setting fixed -Seril monitor LDR nad Servo Motor fixed
    [main.ino]
2024-07-22 upgrate de readme
2024-07-22 - Add DHT11 sensor - Add LED indication for the temperature
2024-07-23 add folder for 3d-files
    [Base middle_x1.stp, Base top_x1.stp, Base_x1.stp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]
2024-07-23 Add files via upload
    Changes: Joints have been inverted to optimize 3d printing
    [Base top_V2_x1.stp, Base_V2_x1.stp]
2024-07-24 File modification: solar panel spin
    Joints adjustment
    [Solar panel spin_V2_x1.stp]
2024-07-31 Assembly guide V1
2024-07-31 Base parts changes
    Addition of holes for small magnets (optional)
    [Base top_V3_x1.stp, Base_V3_x1.stp]
2024-08-09 Add files via upload
    Water static disc modification
    [Water static disc_V2_x2.stp]
2024-09-05 unified code and bug fixes
    [main.ino]
2024-09-16 Add Meadsure Voltage, Add thread processor, Restructure code
2024-09-17 fix voltage input
2024-09-20 Fix speed motor servo and add feature "reconnecting to wifi"
    [main.ino]
2024-09-23 led adafruit send
2024-09-30 adjust servo speed
2024-10-14 change voltage sensor pin2 to pin36
2024-11-13 adjust servo motor and LDR
